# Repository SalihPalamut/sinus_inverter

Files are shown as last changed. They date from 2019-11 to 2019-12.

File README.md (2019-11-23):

# Pure Sinus Inverter
Stm32f103c8t6 Complementery pwm sinus inverter. You can use BluePill.
Compute yours feedback and writing yours codes.

## Theory
18kHz to 50Hz use 360 sinus table
Project use Complementary Mode pwm and H bridge so V0 = duty %50.
 
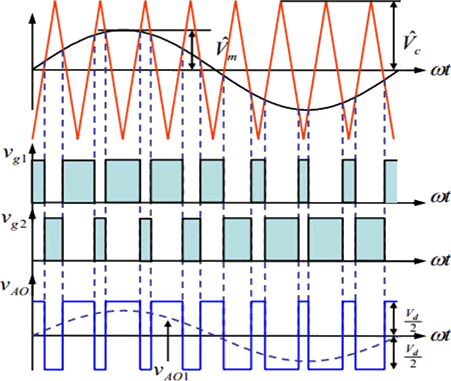
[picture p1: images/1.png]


## Video
https://youtu.be/NGN4gsBzIUE

Running Video (https://youtu.be/NGN4gsBzIUE)
## Circuit
Include Altium, BOM and pdf files.

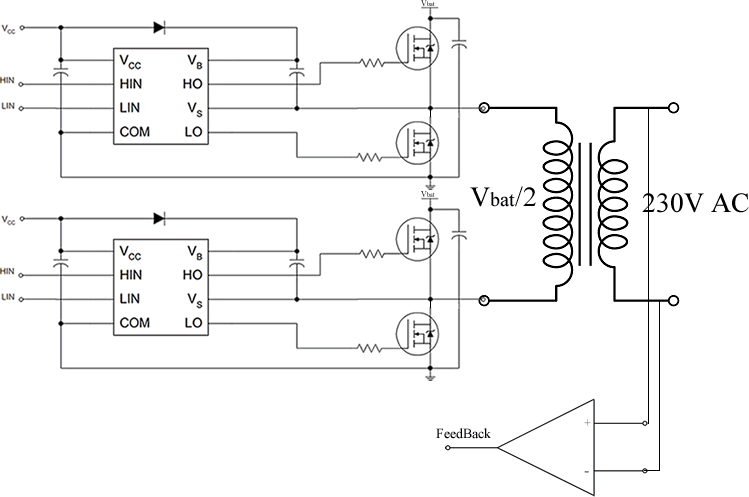
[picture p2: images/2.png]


## Stm32 Settings
+ Debug
	+ Serial
+ ADC
	+ ADC1 An0
+ Timer 1
	+ 18kHz Pwm out 
	+ 1ms DeadTime
	+ Complementary Mode
	+ PA8,9 and PB13,14 pin out
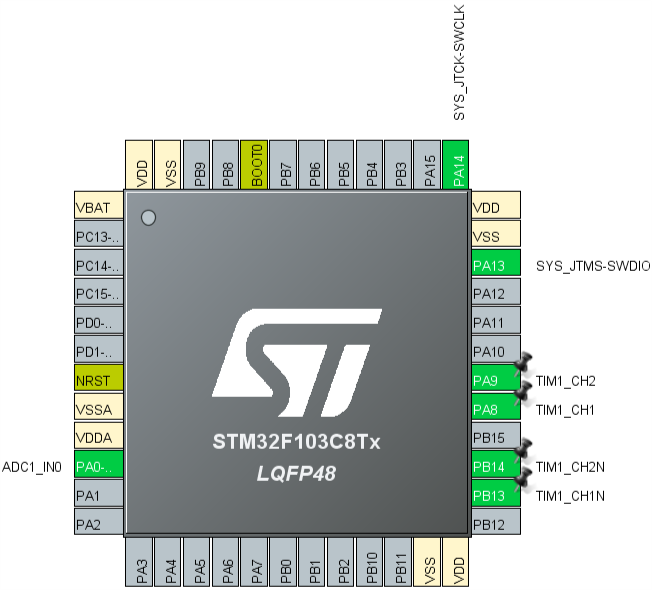
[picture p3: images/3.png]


## Sinus Code
```C
//sinus values 0~179
const float sinus_table[]={
0.000000,0.017452,0.034899,0.052336,0.069756,0.087156,0.104528,0.121869,0.139173,0.156434,0.173648,0.190809,0.207912,0.224951,0.241922,0.258819,0.275637,0.292372,0.309017,0.325568,0.342020,0.358368,0.374607,0.390731,0.406737,0.422618,0.438371,0.453990,0.469472,0.484810,0.500000,
0.515038,0.529919,0.544639,0.559193,0.573576,0.587785,0.601815,0.615661,0.629320,0.642788,0.656059,0.669131,0.681998,0.694658,0.707107,0.719340,0.731354,0.743145,0.754710,0.766044,0.777146,0.788011,0.798636,0.809017,0.819152,0.829038,0.838671,0.848048,0.857167,0.866025,
0.874620,0.882948,0.891007,0.898794,0.906308,0.913545,0.920505,0.927184,0.933580,0.939693,0.945519,0.951057,0.956305,0.961262,0.965926,0.970296,0.974370,0.978148,0.981627,0.984808,0.987688,0.990268,0.992546,0.994522,0.996195,0.997564,0.998630,0.999391,0.999848,1.000000,
0.999848,0.999391,0.998630,0.997564,0.996195,0.994522,0.992546,0.990268,0.987688,0.984808,0.981627,0.978148,0.974370,0.970296,0.965926,0.961262,0.956305,0.951057,0.945519,0.939693,0.933580,0.927184,0.920505,0.913545,0.906308,0.898794,0.891007,0.882948,0.874620,0.866025,
0.857167,0.848048,0.838671,0.829038,0.819152,0.809017,0.798636,0.788011,0.777146,0.766044,0.754710,0.743145,0.731354,0.719340,0.707107,0.694658,0.681998,0.669131,0.656059,0.642788,0.629320,0.615661,0.601815,0.587785,0.573576,0.559193,0.544639,0.529919,0.515038,0.500000,
0.484810,0.469472,0.453990,0.438371,0.422618,0.406737,0.390731,0.374607,0.358368,0.342020,0.325568,0.309017,0.292372,0.275637,0.258819,0.241922,0.224951,0.207912,0.190809,0.173648,0.156434,0.139173,0.121869,0.104528,0.087156,0.069756,0.052336,0.034899,0.017452};
//Every tick call, duty from feedback
void HAL_TIM_Update()
{
	static uint8_t i = 0, j = 1;
	if(duty<10)duty=10;
	if(duty>1990)duty=1990;
	calc_pwm = duty * sinus_table[i];
	if(j)
		{
			TIM1->CCR1 = 2000+calc_pwm;
			TIM1->CCR2 = 2000-calc_pwm;
		}
	else
		{
			TIM1->CCR1 = 2000-calc_pwm;
			TIM1->CCR2 = 2000+calc_pwm;
		}
	i++;
	if(i > 179)
		{
			i = 0;
			j = !j;
		}
}
```

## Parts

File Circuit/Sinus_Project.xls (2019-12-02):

Comment | Description | Designator | Footprint | LibRef | Quantity
4n7 |  | C1, C3, C6, C9, C12 | 1206 | Cap | 5.0
100nF |  | C2, C8, C10, C14, C15, C18, C21, C23, C24, C25, C29, C32 | 1206 | Cap | 12.0
1uF |  | C4, C7, C11, C13, C16, C17, C22, C33 | 1206 | Cap | 8.0
100n |  | C5 | 1206 | Cap | 1.0
20pF |  | C19, C20 | 1206 | Cap | 2.0
Cap |  | C26, C27, C28, C30 | 1206 | Cap | 4.0
100nF |  | C31 | C0805 | Cap | 1.0
Diode 1N4004 | 1 Amp General Purpose Rectifier | D1, D2 | SOD123 | Diode 1N4004 | 2.0
M2_pad |  | Gnd1, M1, M2, Vcc1 | M2_Pad | M2_pad | 4.0
Mavi |  | Ld1 | L1206 | Led | 1.0
Yeþil |  | Ld2 | L1206 | Led | 1.0
Sarý |  | Ld3 | L1206 | Led | 1.0
Kýrmýzý |  | Ld4 | L1206 | Led | 1.0
Header 2 | Header, 2-Pin | P1, P2 | 2p_fml | Header 2 | 2.0
Header 3 | Header, 3-Pin | P3 | HDR1X3 | Header 3 | 1.0
Header 2 | Header, 2-Pin | P4 | HDR1X2 | Header 2 | 1.0
DcFan | Header, 2-Pin | P5 | HDR1X2 | Header 2 | 1.0
Buzzer | Header, 2-Pin | P6 | HDR1X2 | Header 2 | 1.0
psmn6r5-25 |  | Q1, Q2, Q3, Q4 | power-so8 | psmn6r5-25 | 4.0
BC817 | 45 V, 500 mA NPN general-purpose transistors | Q5, Q6 | SOT23 | BC817 | 2.0
250k |  | R1, R2, R7, R8, R9, R10, R11, R12 | 1206 | Resistor | 8.0
3k3 |  | R3 | 0603 | Resistor | 1.0
8k7 |  | R4 | 0603 | Resistor | 1.0
2k2 |  | R5, R6, R25 | 1206 | Resistor | 3.0
4k1 |  | R13, R14 | 1206 | Resistor | 2.0
5k |  | R15 | 1206 | Resistor | 1.0
2.2k |  | R16 | 1206 | Resistor | 1.0
1k |  | R17, R18, R19 | 1206 | Resistor | 3.0
10R |  | R20, R21, R22, R23 | 0603 | Resistor | 4.0
10R |  | R24 | 1206 | Resistor | 1.0
2K2 |  | R26 | 0603 | Resistor | 1.0
Þönt 0.01 Ohm 3W | 0.01 Ohm 3W | R27 | Shont_2512 | Resistor | 1.0
LM1117-12v |  | RG1 | SOT-223 | LM1117 | 1.0
LM1117-5v |  | RG2 | SOT-223 | LM1117 | 1.0
LM1117-3v3 |  | RG3 | SOT-223 | LM1117 | 1.0
MCP6022 |  | U1 | SOP-8L | MCP6022 | 1.0
IR2301 |  | U2, U3 | SOP-8L | IR2301 | 2.0
STM32F103C8T6 |  | U4 | LQFP48 | STM32F103C8T6 | 1.0
M3_Vida |  | V1, V2 | M3_Vida | M3_Vida | 2.0
8MHz |  | Y1 | xtal | Xtal | 1.0

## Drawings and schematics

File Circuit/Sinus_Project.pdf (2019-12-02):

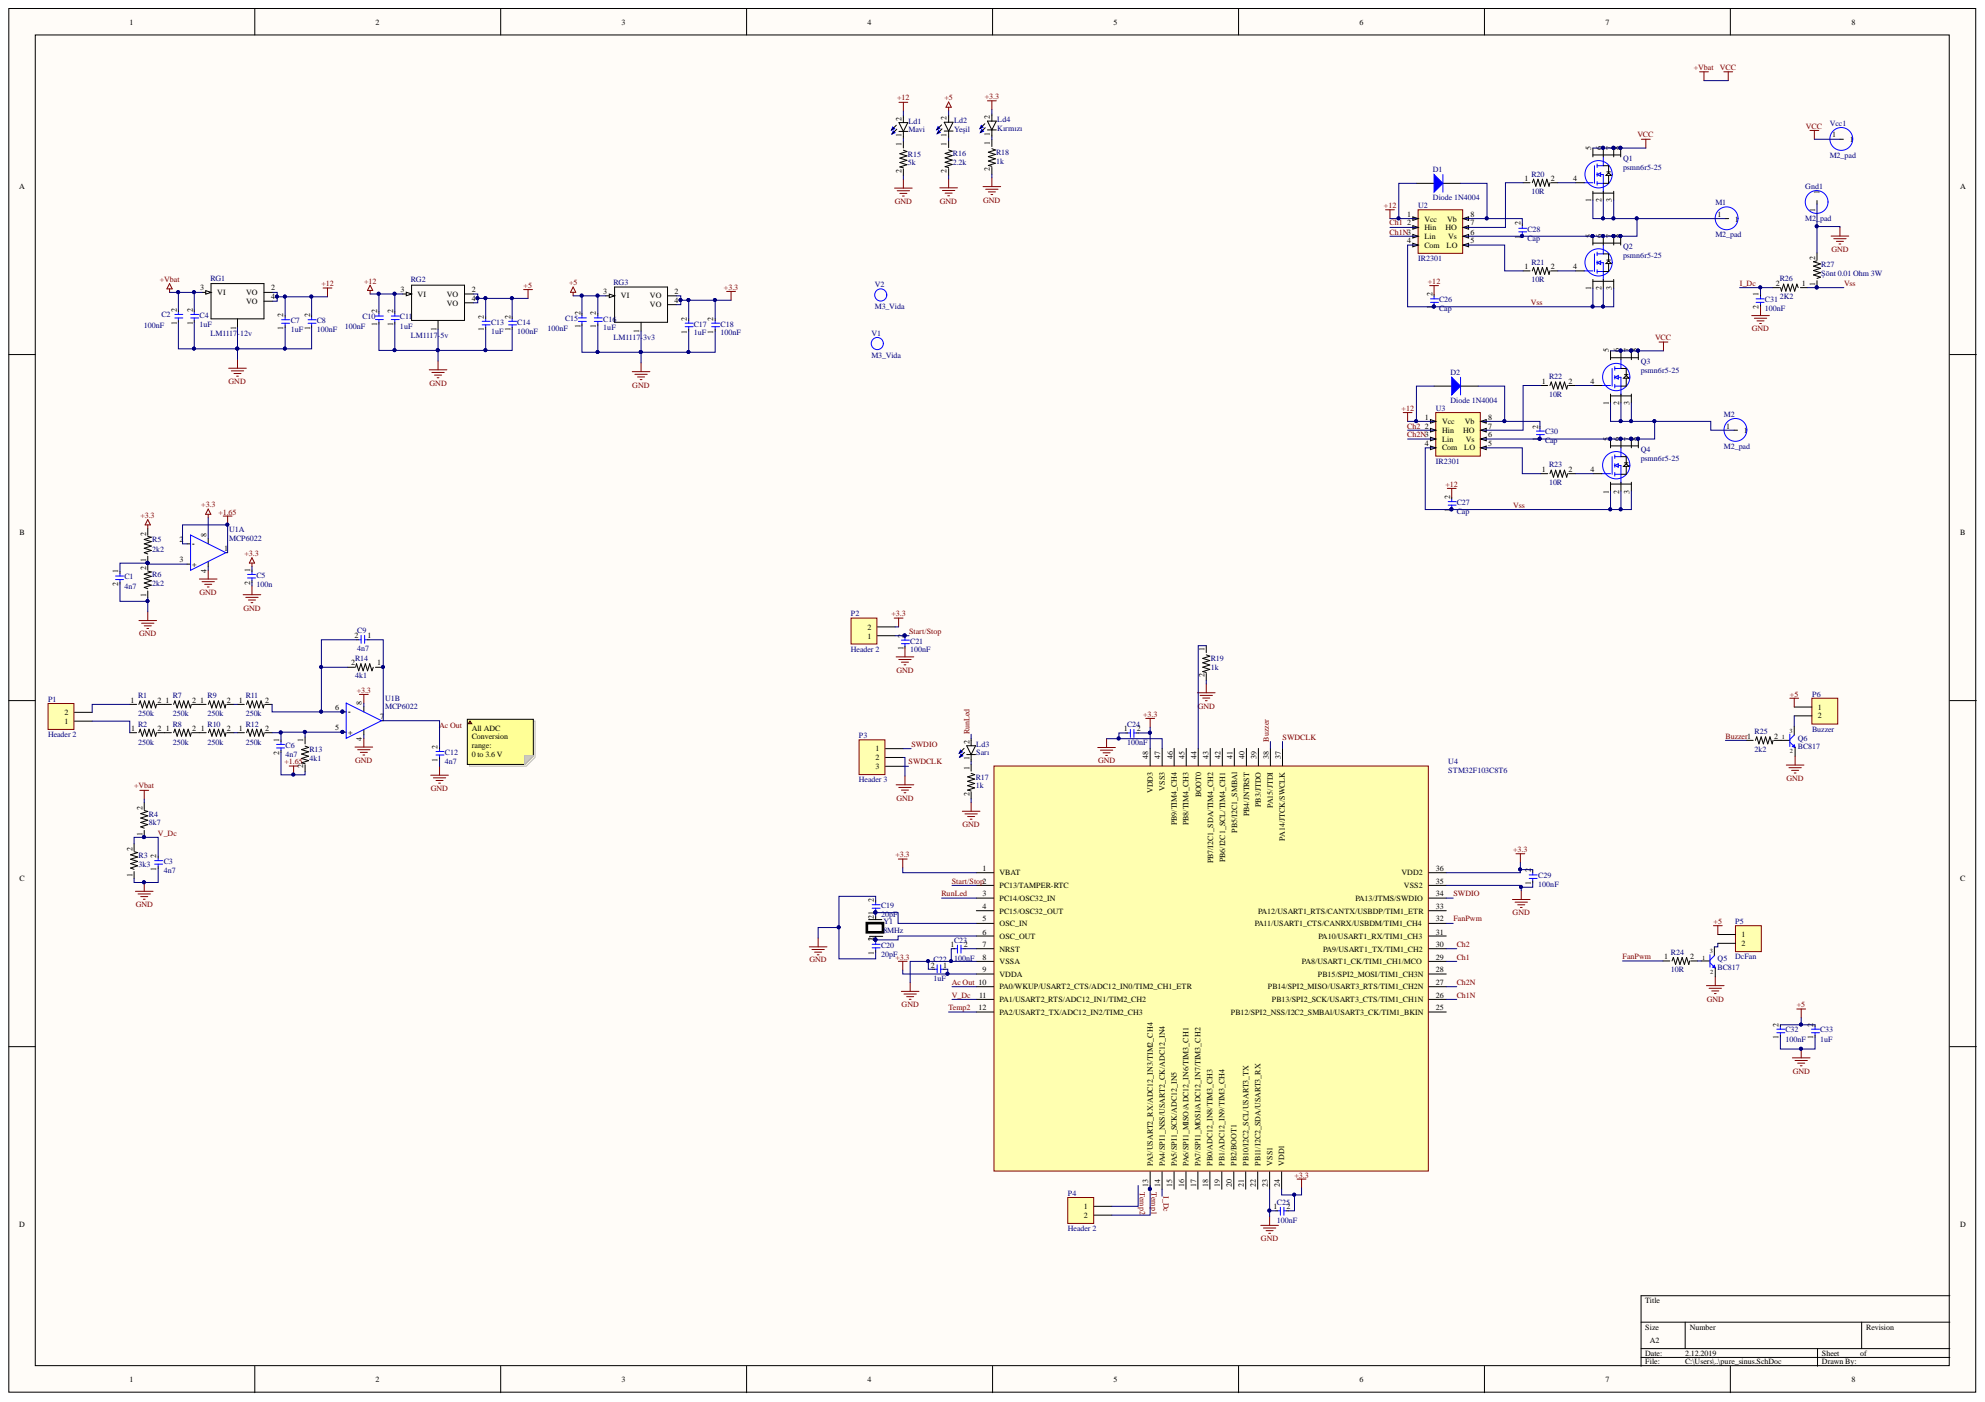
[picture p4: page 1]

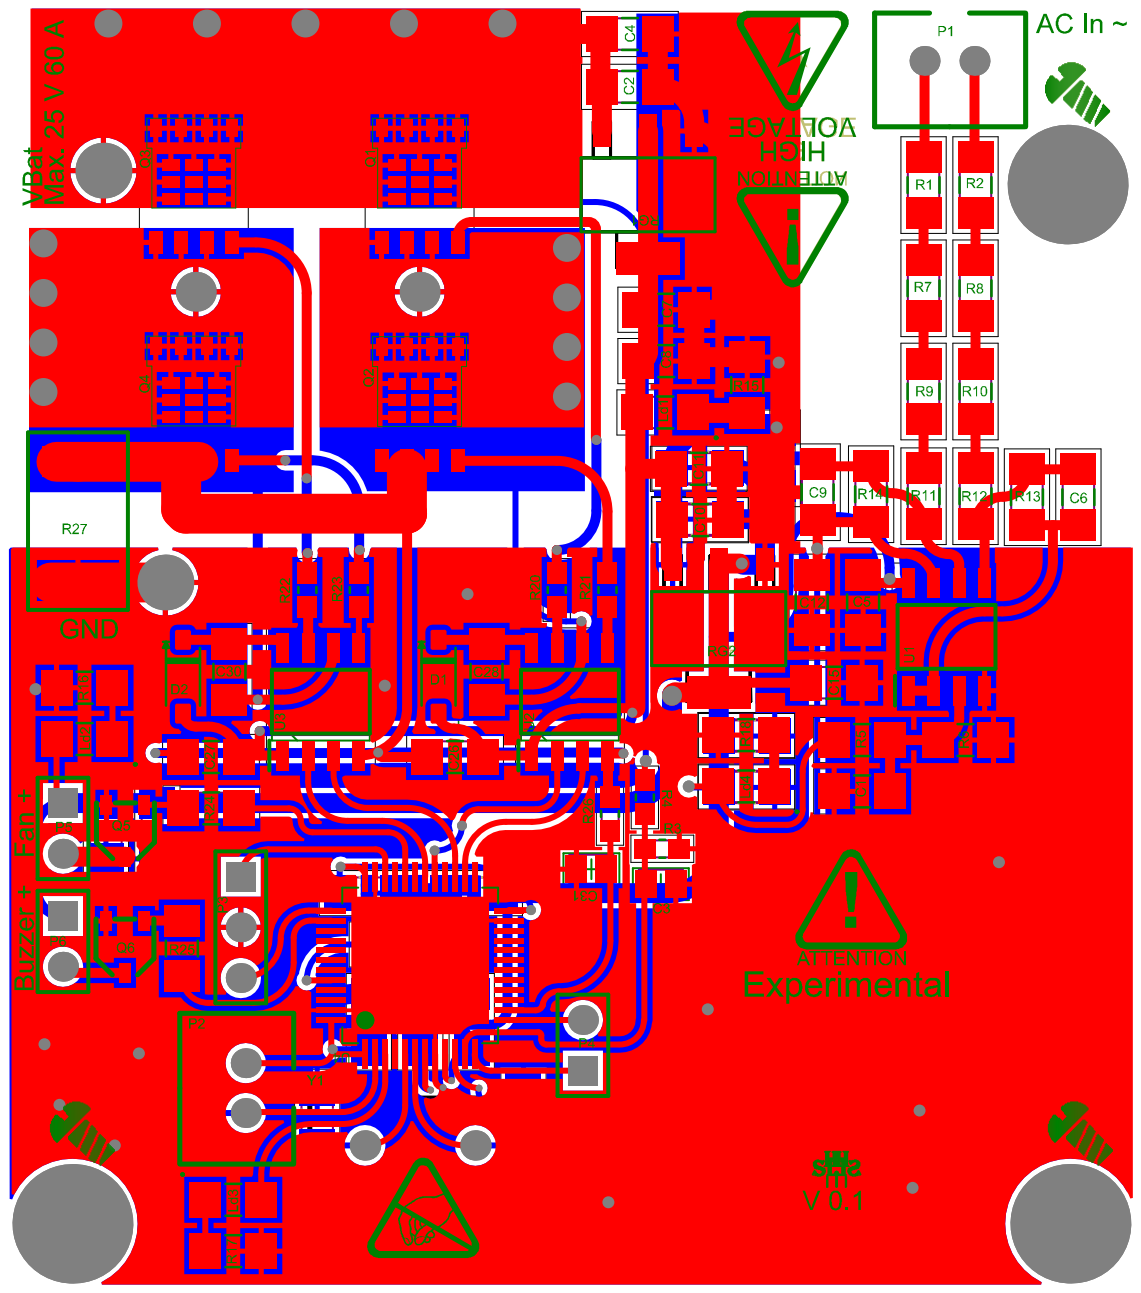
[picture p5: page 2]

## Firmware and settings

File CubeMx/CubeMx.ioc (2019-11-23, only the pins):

Mcu.UserName=STM32F103C8Tx
PA0-WKUP.Signal=ADCx_IN0
PA13.Signal=SYS_JTMS-SWDIO
PA14.Signal=SYS_JTCK-SWCLK
PA8.Signal=S_TIM1_CH1
PA9.Signal=S_TIM1_CH2
PB13.Signal=TIM1_CH1N
PB14.Signal=TIM1_CH2N

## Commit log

2019-11-23 Create Keil uVision project 1)Add pwm codes 2)edit CubeMx Project
2019-11-23 Add circuit files
    [pure_sinus.SchDoc, pure_sinus.xls]
2019-12-02 Add PCB project V 0.1
    [Sinus_Project.PrjPCB, Sinus_Project.xls, pure_sinus.PcbDoc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]
